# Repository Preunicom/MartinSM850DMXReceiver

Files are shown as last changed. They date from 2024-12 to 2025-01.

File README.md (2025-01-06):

# Martin SM850 DMX-Receiver
Adapter from DMX to Martin fog control for Martin SM850

---

## User Manual
### Status LEDs
- Blue LED (Power_LED/"Power")
  - LED ON: Circuit powered
  - LED OFF: Circuit not powered
- Green LED (DIN_Ready_LED/"Ready")
  - LED ON: Fog machine ready
  - LED OFF: Fog machine not ready or not connected
- White LED (Fogging_LED/"Fogging")
  - LED ON: Currently sending a fogging signal
  - LED OFF: Currently not sending a fogging signal
- Green LED (Valid_Address_LED/"Adr. valid")
  - LED ON: DMX address valid
  - LED OFF: DMX address invalid

### DMX control
The fog machine is fogging when
- the value of the set DMX channel is greater than 250 and
- the set dmx address is valid and 
- the fog machine is ready (the fog signal will be sent independently of the ready state of the fog machine but the fog machine will deny it)

### DMX address
To set the DMX address use the 10 channel DIP Switch.
Each switch represents a number (see next table).

| Switch | 1 | 2 | 3 | 4 | 5  | 6  | 7  |  8  |  9  | 10  |
|:---:|:-:|:-:|:-:|:-:|:--:|:--:|:--:|:---:|:---:|:---:|
| Number | 1 | 2 | 4 | 8 | 16 | 32 | 64 | 128 | 256 | 512 |

The fog machine only needs one channel so the lowest possible DMX address is 1 and the highest possible DMX address is 512.
Addresses outside this range are invalid. This is shown by the green status LED next to the address input switches.

### Power
The power is taken by the DIN connection with the fog machine.

### Connecting
Connect the DIN connector with a 5 pin 180° DIN cable with the "WIRELESS CONTROLLER" connector of the fog machine.
Connect the DMX connector with one or two 3 pin DMX cable with your DMX bus topology.

---

## Martin SM850 Specifications
### Pin assignment of wireless controller DIN Connector

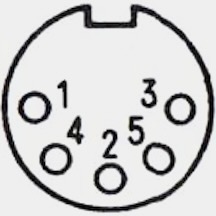
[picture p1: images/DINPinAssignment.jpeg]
Pin Layout


The picture is looking at the female connector in the fog machine.

| Pin | wireless receiver wire color | function | Voltage  |
|:---:|:---:|:---:|:---:|
|  1  | red | NOT READY / READY | 0V / +5V |
|  2  | yellow | VCC | +5V |
|  3  | none | none | none |
|  4  | blue | FOGGING | 0V |
|  5  | green | GND | 0V |

Short pin 4 and 5 to fog. <br>
Connect a LED directly connected to pin 1 (+/anode) and 5 (-/cathode) to get ready state.

---

## Hardware
### Components
#### Microcontroller
> 1x Arduino Pro Mini (ATmega328P) with 5V and 16MHz.

#### RS485 Converter
> 1x MAX485

#### Sockets
> 1x 5 pin 180° DIN socket

> 1x 3 pin DMX socket female

> 1x 3 pin DMX socket male

#### Other components
> 1x 10 channel DIP switch --> Input for DMX address

> 1x Transistor (e.g. S8050) --> Switching the fogging machine

> 2x LED green --> In-/Valid DMX address set, fog machine ready <br>
> 1x LED white --> Fogging indicator <br>
> 1x LED blue --> Power

> 4x 220 Ohm resistor --> Current limiting resistors for LEDs and transistor

> 1x 120 Ohm resistor --> Termination resistor

> 1x 100 nF capacitor --> Power stabilisation for MAX485 (coupling capacitor)

### Circuit design
#### DIP Switch
Least significant bit is Arduino[D3]. <br>
Most significant bit is Arduino[A5].
```
Arduino[D3] <-> DIP[1] <-> GND
Arduino[D4] <-> DIP[2] <-> GND
Arduino[D5] <-> DIP[3] <-> GND
Arduino[D6] <-> DIP[4] <-> GND
    
Arduino[A0] <-> DIP[5] <-> GND
Arduino[A1] <-> DIP[6] <-> GND
Arduino[A2] <-> DIP[7] <-> GND
Arduino[A1] <-> DIP[8] <-> GND
Arduino[A4] <-> DIP[9] <-> GND
Arduino[A5] <-> DIP[10] <-> GND
```
#### Status LEDs
```
Arduino[D7] <-> LED green <-> 220Ohm resistor <-> +5V
Arduino[VCC] <-> LED blue <-> 220Ohm resistor <-> GND
Arduino[D8] <-> LED white <-> 220Ohm resistor <-> GND
DIN[1] <-> LED green <-> GND
```

#### MAX485
```
MAX485[VCC] <-> Arduino[VCC]
MAX485[VCC] <-> 100nF capacitor <-> MAX485[GND]
MAX485[B] <-> DMX[2]
MAX485[A] <-> 120Ohm resistor <-> MAX[B]
MAX485[A] <-> DMX[3]
MAX485[GND] <-> Arduino[GND]
MAX485[GND] <-> DMX[1]

MAX485[RO] <-> Arduino[RXI]
MAX485[!RE] <-> Arduino[GND]
MAX485[DE] <-> Arduino[GND]
MAX485[DI]: <unconnected>
```

#### DIN Socket
```
DIN[4] <-> transistor[collector]
Arduino[D8] <-> 220Ohm resistor <-> transistor[base]
transistor[emitter] <-> GND
DIN[2] <-> Arduino[VCC]
DIN[5] <-> GND
```

### Schematics
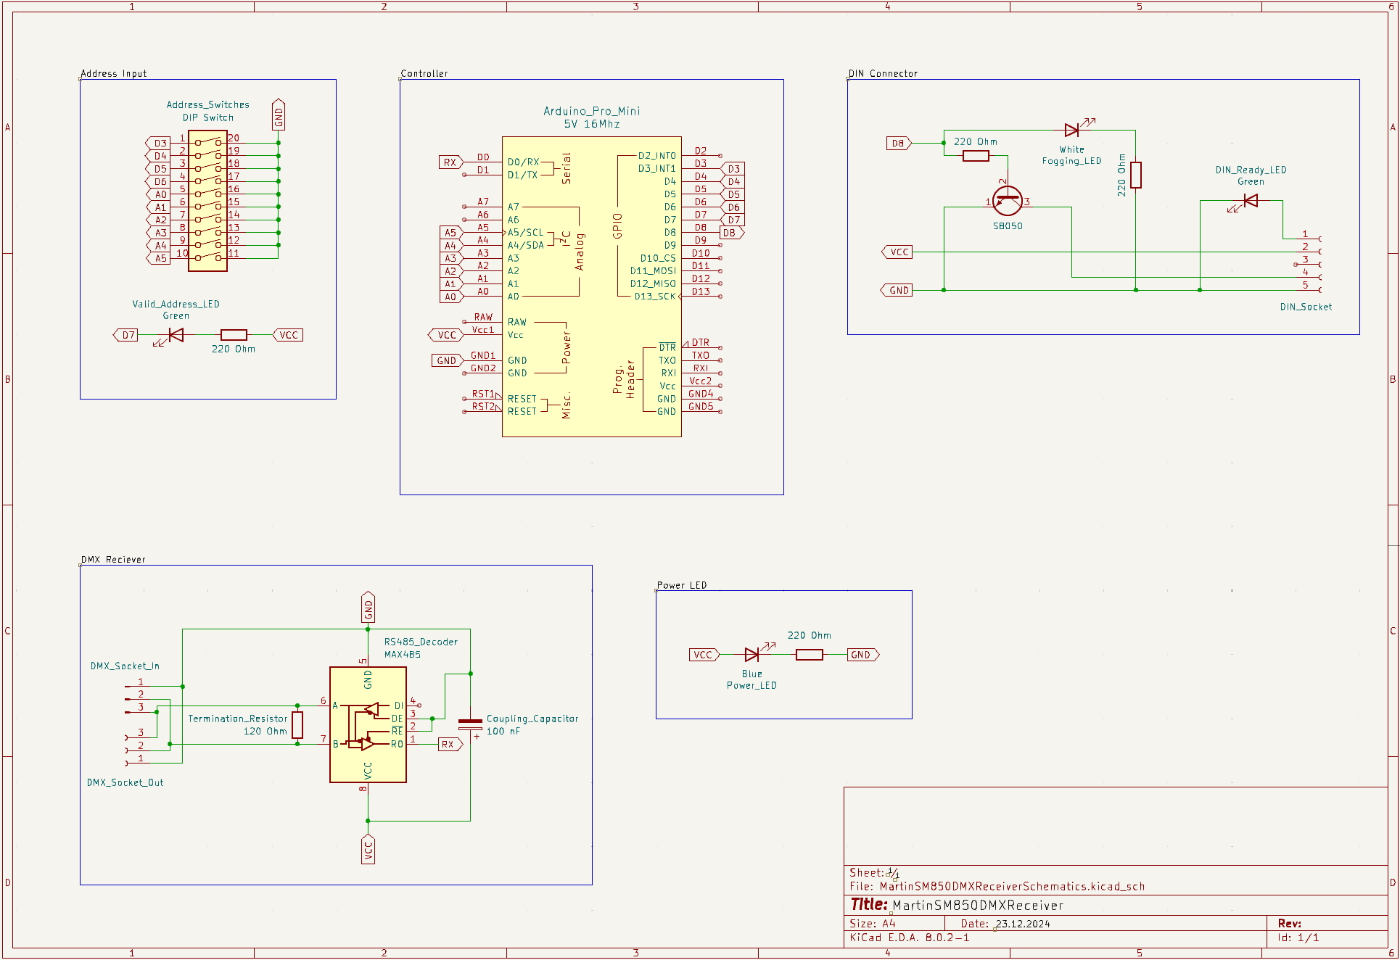
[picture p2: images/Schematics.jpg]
Schematics


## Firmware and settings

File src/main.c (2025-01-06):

#include <util/delay.h>
#include "../lib/DMX_Switch/src/DMX_Switch.h"
#include "../lib/MartinSM850FogMachine/src/MartinSM850FogMachine.h"

int main() {
    init_DMX();
    init_DIN();
    while(1) {
        if(get_DMX_value() > 250 && is_valid_DMX_address()) {
            // DMX value "On" path
            fog();
        } else {
            // DMX value "Off" or DMX address invalid path
            stop_fog();
        }
        // Perfect would be 1 ms because 250K Baud and 512 Channel per Universe.
        // This is very fast, and we don't need this high speed,
        // because we don't change the signal at this high rates with a fader.
        // Even if the signal change reaction would be delayed by 20 ms we won't recognize it,
        // and it reduces a lot of load on the microcontroller.
        _delay_ms(20);
    }
}

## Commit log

2024-12-02 Created Schematics
    [MartinSM850DMXReceiverSchematics.kicad_sch]
2024-12-02 Added picture of Schematics
2024-12-25 Updated README and added Schematics and User manual
    [MartinSM850DMXReceiverSchematics.kicad_sch]
2025-01-05 Schematics and fixes (#7)
    * BugFix: invalid DMX address does stop fogging now
    * Schematics: added schematics
    [MartinSM850DMXReceiverSchematics.kicad_sch]
